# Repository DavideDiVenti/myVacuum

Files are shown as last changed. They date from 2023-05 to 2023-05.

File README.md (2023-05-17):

# myVacuum
La conception d'un projet s'est déroulé dans le cadre d'un cours de bureaux d'études. Le projet en question est un aspirateur digital. 
Le rendu 3D du projet peut être directement visionné en cliquant sur [ce lien hypertexte](https://a360.co/3LSl4pl) (ouvrez ensuite *depuis le navigateur*).

## Introduction
Le projet en question consiste en un aspirateur doté de fonctionnalités numériques supplémentaires. Comme tout aspirateur domestique, il a pour fonction principale d'aspirer les miettes, la poussière, le sable, etc. Toutefois, contrairement à ses homologues, myVacuum est capable de fournir à son utilisateur un état de santé en temps réel grâce à un écran. Cet état inclut des informations telles que la température interne de l'appareil, le niveau de remplissage du réservoir, la qualité de l'air aspiré, la vitesse du ventilateur, et bien d'autres encore.

L'utilisateur peut contrôler l'aspirateur à partir d'une interface utilisateur. Cette dernière prend la forme d'une télécommande filaire équipée d'un petit écran et de 4 boutons poussoirs. L'interface comprend plusieurs menus préprogrammés, notamment une zone permettant de visualiser et de commander l'état de l'appareil (puissance d'aspiration), ainsi qu'une autre zone permettant d'acquérir des données et de créer des graphiques des données lues par les capteurs en temps réel. 

## Le répertoire [*myVacuumCode*](https://github.com/DavideDiVenti/myVacuum/tree/main/myVacuumCode)
### Code du microcontroleur
L'aspirateur intègre le microcontrôleur ESP32. Les codes téléversés sont dans le répertoire [myVacuumCode](https://github.com/DavideDiVenti/myVacuum/tree/main/myVacuumCode). Ce-dernier assemble tous les périphériques de l'aspirateur (voir [Rapport](https://github.com/DavideDiVenti/myVacuum/blob/main/Documents/Rapport.pdf)) afin de centraliser le tout.

### Design de l'écran
A noter que le rendu final du projet n'aurait pas pu etre possible sans l'utilisation d'un logiciel en particulier. Ce logiciel est un ancien projet que j'ai développé expressément pour l'aspirateur : 
* L'idée de ce logiciel est que l'utilisateur puisse créer des icones et animations de ces-derniers en pixelart. 
* A chaque interraction le logiciel exporte l'image sous forme d'une chaine hexadécimale et/ou binaire. 
* L'utilisateur peut ensuite copier cette chaine et l'introduire dans le code de son microcontroleur.
* Le code du microcontroleur interpretera cette chaine hexadécimale ou binaire afin de créer des objets de classe respectif à chaque chaine (icone d'un ventilateur, d'un termomètre, d'un buzzer, ...). 
* La [classe](https://github.com/DavideDiVenti/myVacuum/blob/main/myVacuumCode/myClass_DrawOnTheScreen.cpp) pourra ensuite proposer divers méthodes afin d'afficher les pixels sur l'écran correspondant à l'objet en question.

Ce processus permet notamment de créer des animations de plusieurs frames d'un meme objet :
<p align="left">
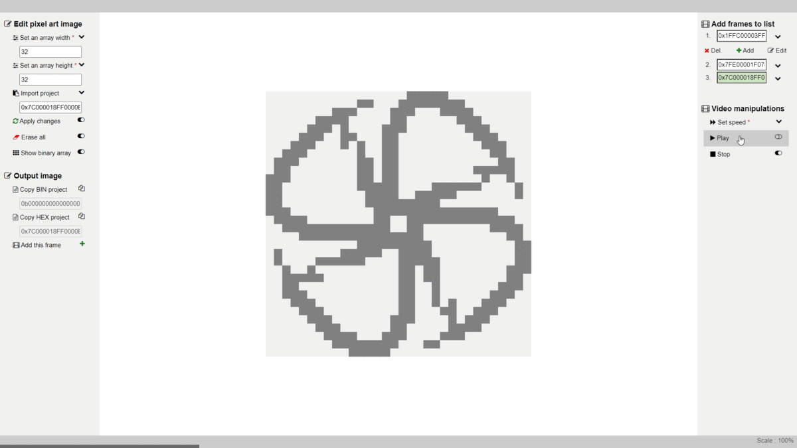
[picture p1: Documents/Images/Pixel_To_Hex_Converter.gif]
  
</p>
Le logiciel est disponible depuis ce lien : https://davidediventi.github.io/PixelToHexConverter/

## Le répertoire [*Documents*](https://github.com/DavideDiVenti/myVacuum/tree/main/Documents)
Divers documents sont situés dans ce répertoire [Documents](https://github.com/DavideDiVenti/myVacuum/tree/main/Documents). Des informations supplémentaires s'y trouvent :
* Un dossier [Impressions_3D](https://github.com/DavideDiVenti/myVacuum/tree/main/Documents/Impressions_3D) contenant l'entièreté des fichiers d'impression au format stl. 
* Un dossier [Images](https://github.com/DavideDiVenti/myVacuum/tree/main/Documents/Images) contenant quelques aperçuts finaux du projet (PCB, Mécanique, Schémas, ...).
* Un fichier [Rapport](https://github.com/DavideDiVenti/myVacuum/blob/main/Documents/Rapport.pdf) correspondant au rapport du projet sous le format pdf. Dedans se trouve l'entièreté du contenu (schémas, développements techniques, ...) ainsi qu'un tableau des pinouts de l'ESP32.

## Youtube
Il est toujours plus ludique d'observer le projet sous forme de vidéos.

### Démonstration du projet :
Dans cette vidéo, l'aspirateur aspire plusieurs type de déchets (copeaux d'aluminium, terre, copeaux de bois, ...).

Vidéo postée prochainement...

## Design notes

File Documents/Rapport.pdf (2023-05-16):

## MYVACUUM, L’ASPIRATEUR INTELLIGENT

Conception Mécanique, Électronique, Traitement De Signal, Programmation, …

### Par DI VENTI Davide 60456@etu.he2b.be

RÉSUMÉ

Le projet en question consiste en un aspirateur doté de fonctionnalités numériques supplémentaires. Comme tout aspirateur domestique, il a pour fonction principale d'aspirer les miettes, la poussière, le sable, etc. Toutefois, contrairement à ses homologues, myVacuum est capable de fournir à son utilisateur un état de santé en temps réel grâce à un écran. Cet état inclut des informations telles que la température interne de l'appareil, le niveau de remplissage du réservoir, la qualité de l'air aspiré, et bien d'autres encore.

L'utilisateur peut contrôler l'aspirateur à partir d'une interface utilisateur. Cette dernière prend la forme d'une télécommande filaire équipée d'un petit écran et de 4 boutons poussoirs. L'interface comprend plusieurs menus préprogrammés, notamment une zone permettant de visualiser et de commander l'état de l'appareil, ainsi qu'une autre zone permettant d'acquérir des données et de créer un système de logs¹
à partir d'une carte SD.

Tout comme les aspirateurs domestiques classiques, myVacuum est équipé d'une fonction permettant de régler la puissance d'aspiration. Toutefois, contrairement aux autres modèles, cette fonction est entièrement numérique, ce qui la rend plus précise. De plus, il dispose d'un tachymètre intégré qui fournit un retour sur la vitesse du ventilateur.

### 1. INTRODUCTION

Ce rapport présente la conception et la réalisation d'un aspirateur digital, en mettant l'accent sur les différentes parties mécaniques, électroniques et de programmation du système. La partie mécanique est abordée en premier lieu, en décrivant la conception de pièces spécifiques telles que des adaptateurs en plastique et en métal. Ensuite, la partie électronique est examinée, mettant en lumière les choix de composants ainsi que le traitement du signal du capteur, un point central du projet. Le traitement du signal est effectué en utilisant des principes tels que le filtrage, l'amplification et le registre à décalage. Enfin, la partie programmation est présentée en détail, expliquant le fonctionnement final du code et incluant un lien vers le dépôt GitHub où celui-ci est disponible. Des schémas électroniques et

1Logs : Sous forme d’un tableau, il s’agit d’une suite séquentielles de valeurs acquises par des capteurs ou autre en fonction du temps. Cela peut se référer à un historique. Chaque données est stockée tous les laps de temps.

mécaniques détaillés du système sont également fournis dans les annexes du rapport.

L'objectif premier de ce rapport est de présenter un produit sortant d'un bureau d'études, qui intègre des systèmes embarqués de manière technique.

### 2. DESCRIPTION DU PROJET

Le projet est subdivisé en quatre grandes parties distinctes. Chacune de ces parties a nécessité des prérequis spécifiques ainsi qu'une durée de conception relativement similaire à celle des autres parties.

### 2.1. Mécanique

La mécanique est un aspect essentiel de ce projet. Chaque élément a été préalablement conçu en 3D, allant des différents adaptateurs jusqu'aux joints d'étanchéité. Les adaptateurs, qui sont imprimés en 3D en PLA, ont été créés pour servir de supports pour les capteurs, pour les systèmes d'emboîtement (entre filtre, ventilateur, réservoir, tube d'aspiration, etc.), pour les connecteurs électroniques avec détrompeurs, etc. Le filtre, pour sa part, est également imprimé en 3D. Sa structure est conçue pour accueillir un tissu carbonisé servant de filtre à air. De même, l'interface utilisateur possède un socle imprimé en 3D. Les joints d'étanchéité sont également imprimés, mais cette fois-ci en TPU, un caoutchouc adapté pour l'extrusion des imprimantes 3D.

En outre, j'ai utilisé une CNC pour découper une pièce : il s'agit d'une plaque en acrylique positionnée à la base du filtre. Cette plaque permettra à un capteur de pouvoir émettre une lumière et recevoir sa réflexion tout en étant protégé des déchets dans le réservoir (capteur de niveau de remplissage du réservoir). Le réservoir de l'aspirateur est également fabriqué en acrylique. Il s'agit d'un tube cylindrique de 100 mm de diamètre.

Enfin, une fois toutes ces pièces assemblées, j'ai remarqué que l'aspirateur avait tendance à tomber latéralement à plusieurs reprises. J'ai donc été contraint de trouver une solution, et j'ai décidé de concevoir un socle en aluminium à l'aide d'un tour à métaux. Cette pièce s'emboîte dans le bas du réservoir, permettant ainsi de fermer le réservoir et de descendre le centre de gravité de l'aspirateur. Cette solution a été la plus adaptée et satisfaisante pour moi, étant passionné depuis mon enfance par l'usinage de pièces industrielles.

En prenant en compte le temps de conception de chaque pièce mécanique (temps d'impression 3D non inclus), cela représente plus de 22 heures de travail.

### 2.2. Électronique

Dans ce projet, l'électronique utilise une architecture basée sur une unité de contrôle. Cette carte électronique
centralise | les | données | provenant | de | différents
périphériques tels que les capteurs, le ventilateur et l'écran, pour les traiter, les afficher, les stocker, etc.

Un microcontrôleur ESP32 a été choisi pour cette unité de contrôle. Toutes les broches du microcontrôleur ont été utilisées afin de tirer pleinement parti de ses capacités. L’annexe 7 présente les périphériques connectés (ou transistorisés) à ce microcontrôleur, je vous invite à la prendre.

Chaque périphérique est justifié et joue un rôle crucial dans le cadre de ce projet. Le buzzer permet d'alerter l'opérateur en cas de détection d'un code d'erreur. Par exemple, si l'aspirateur aspire de la matière brûlée (détectée par le DHT11 et le capteur de gaz MQ-2), de la matière humide (par le DHT11), ou un gaz nocif pour la santé humaine (par le capteur de gaz MQ-2), le buzzer émet une alerte. D'autres situations peuvent également survenir, telles que le remplissage du réservoir (capteur de distance VL6180X), la nécessité de nettoyer le filtre (vitesse du ventilateur trop faible), ou encore la saturation de la carte SD.

Le relais fonctionne selon le même principe que celui intégré dans les aspirateurs industriels, à savoir une prise 230VAC destinée à connecter une machine-outil telle qu'une scie sauteuse, une foreuse ou une défonceuse. En d'autres termes, si le périphérique 230VAC est activé, l'aspirateur s'allume. Dans le cas de myVacuum, ce principe est repris, mais sous une forme miniaturisée avec un relais.

Le ventilateur utilisé (bg0903-b049-p0s) provient d'un PC Dell fixe où il occupait la place du ventirad. L'ensemble du projet est dimensionné en fonction de ce ventilateur, qui est un ventilateur 12VDC comportant 4 broches dont deux pour l'alimentation 12V, une pour le tachymètre, et une pour la commande PWM. Le « Fan MOSFET » affiché dans l’annexe 7 du ventilateur, est un simple transistor MOSFET que j’ai ajouté permettant de couper ou de fournir l'alimentation 12V externe au ventilateur. En effet, même en forçant un état logique bas (0V) à la commande PWM du ventilateur, sa vitesse (tr/min) ne descend pas à zéro, mais atteint plutôt un seuil minimum de XX tr/min.

En prenant en compte le temps nécessaire à la réflexion (choix des composants) et à la conception électronique (schémas électroniques et conception du PCB), le temps total de travail estimé s'élève à plus de 16 heures.

### 2.3. Traitement de signal

Le traitement du signal réalisé dans ce projet est la partie la plus électronique de la machine concernée. Il est effectué à la sortie du tachymètre du ventilateur, de manière à ce que l’ESP32 puisse lire la vitesse sans qu'il y ait de nombreuses erreurs ni de latences. Les étapes suivantes décrivent le dimensionnement des étages de traitement du signal tachymètre.

Avant toute chose, il convient de noter que ce ventilateur envoie 2 signaux logiques par tour.

Le premier étage de traitement du signal vise à transmettre ces signaux avec une logique de 0V à 3,3V (ce qui n'est pas le cas par défaut). Étant donné que le capteur intégré est à effet Hall, l'intensité du signal tachymètre varie en fonction de la vitesse. Plus la vitesse est élevée, plus l'intensité du signal augmente en tension (de 0 à 1,8V), ce qui peut perturber la lecture de la vitesse. Il est donc nécessaire de procéder à un étage d'amplification. Toutefois, avant cela, il est préférable de filtrer les parasites potentiels (pics de tension à très
haute | fréquence) | susceptibles | de | "brouiller"
l'amplification. Pour ce faire, un simple filtre passe-bas RC est suffisant. 'ai dimensionné le filtre de telle sorte que la fréquence de coupure soit d'environ 5 kHz, qui est la fréquence maximale du tachymètre du ventilateur. Ensuite, par expérimentation, j'ai essayé différentes valeurs de R et C pour obtenir une enveloppe de signal filtré adaptée à mes besoins, finalement en utilisant C = 50 nF et R = 2 kΩ, j'ai obtenu un filtrage opérationnel.

Une fois le filtrage terminé, j'ai procédé à l'amplification en utilisant un amplificateur opérationnel (AOP) que j'ai utilisé en tant que comparateur, tel un trigger de Schmitz. Étant donné que le signal filtré possédait un offset de 400 mV, il était important d'éliminer cet offset avant l'amplification. Pour ce faire, j'ai utilisé une tension de référence provenant d'un pont diviseur de tension pour éliminer l'offset par le biais du V- de l'AOP, évitant ainsi que l'offset ne s'amplifie. La tension de référence a été fixée à 800 mV pour garantir que l'offset ne serait pas pris en compte à la sortie du comparateur. Le signal filtré du tachymètre (V+) et la tension de référence (V-) ont été comparés, et seule la tension supérieure à 800 mV a été copiée en sortie. Le signal de sortie du comparateur a atteint un niveau logique équivalent à l’alimentation de l’AOP (0V-3.3V).

Cependant, une problématique persiste en dépit de l'aspect impeccable du signal, carré et net. En effet, la vitesse du signal demeure trop rapide pour être traitée de manière satisfaisante par l'ESP32. Bien que le microcontrôleur puisse traiter et convertir la vitesse du signal en tr/min, un facteur important doit être pris en compte : la latence du programme. À mesure que le programme gère davantage de périphériques, des latences se produisent, entraînant un délai de quelques millisecondes à la fin de la boucle. Une latence de quelques millisecondes (1ms à 20ms) est considérable, surtout si le microcontrôleur doit lire un signal à haute fréquence. L'oscilloscope a mesuré une fréquence de 1250Hz pour le signal filtré et amplifié, ce qui correspond à une période de signal de 800µs. Cela équivaut à une vitesse de rotation du ventilateur de 5500 tr/min.

Un deuxième étage de traitement de signal s’est donc imposé, celui permettant de diminuer la fréquence du signal, tout en restant beau, carré et propre. Pour ce faire, il n’y a rien de plus efficace que de l’électronique ancienne : le registre à décalage. J'ai disposé d'un registre à 8 bits, ce qui m'a permis de diviser la fréquence du signal par 8, résultant en une période de 6,4 ms au lieu de 800 µs. Cette solution est largement suffisante pour mon application. Afin d'assurer le bon fonctionnement de cette idée subite, j'ai simulé ce principe et procédé à plusieurs essais et erreurs. Heureusement, le résultat a été couronné de succès.

En outre, compte tenu du temps nécessaire à l'étape de dimensionnement et aux tests requis pour ces traitements de signaux, le temps total de travail s'élève à plus de 11 heures.

### 2.4. Programmation

Dans le but d'améliorer la compréhension et la simplicité du code, j'ai procédé à l'importation de la bibliothèque Arduino. Cette démarche m’évite de concevoir mes propres méthodes de classe pour effectuer des opérations élémentaires, telles que l'attribution d'une broche en tant que sortie ou entrée, l'affichage de données dans la console et la gestion des interruptions, etc.

2.4.1. Affichage dans l’écran TFT

En complément de cette bibliothèque, le code est doté d'une classe que j'ai élaborée. Cette dernière me permet de créer des icônes et des animations personnalisées sur l'écran TFT. L'objectif est de pouvoir générer plusieurs objets (widgets : icône de ventilateur, icône de thermomètre, ...) et les afficher avec la latence la plus minimale possible.

Afin d'atteindre cet objectif, je n'enregistre pas les images au format PNG, JPG ou autre sur la carte SD, mais plutôt dans un format personnalisé et léger : une chaîne de caractères. À partir de cette chaîne, ma classe décode les données et affiche l'image correspondante pixel par pixel en couleur.

La déclaration de la chaîne de caractères est précédée par les dimensions (en pixels) de l'image à afficher :

int myIconeWidth, myIconeHeight = 16, 16;

String myIcone = "7C00820101014901490FF96 805DFE41407D3F8510851079080206EC02A80444";

Ensuite, ces trois variables sont insérées pour la création de l'objet de ma classe. La chaîne hexadécimale est ensuite convertie en binaire, ce qui entraîne une augmentation de sa longueur quatre fois supérieure. Ligne par ligne et colonne par colonne, la chaîne binaire est parcourue, et la classe affiche des pixels aux coordonnées correspondantes là où des "1" sont présents, tandis qu'elle n'affiche rien là où des "0" sont présents (comme illustré ci-dessous dans la figure 1) :

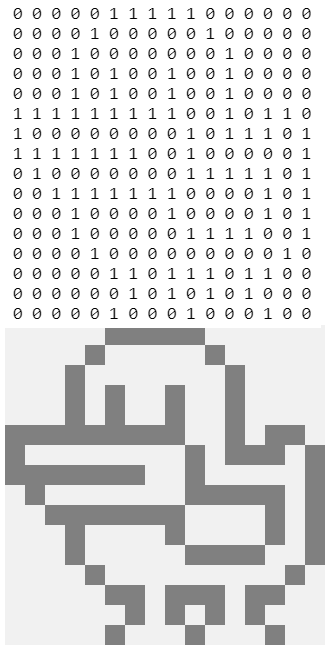
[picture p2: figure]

Figure 1. Processus d’affichage dans l’écran TFT

Cependant, il n'est pas possible pour un être humain d'écrire intuitivement cette chaîne de caractères. Il est donc nécessaire d'effectuer l'inverse du processus. À cet effet, j'ai développé un logiciel en JavaScript qui me
permet | de | générer | la | chaîne | de | caractères
hexadécimale/binaire à partir d'un espace de travail de dessin en PixelArt. Les détails de fonctionnement de ce logiciel ne seront pas abordés dans ce rapport, car cela s'éloignerait du sujet principal. J'ai hébergé ce logiciel sur GitHub, et il est directement accessible via le lien suivant :

https://davidediventi.github.io/PixelToHexConverter/

Le plus grand défi de ce projet a été de surmonter les latences du microcontrôleur, et cette classe combinée à ce logiciel ont joué un rôle clé pour résoudre ce problème.

2.4.2. Acquisitions de données des capteurs

En parallèle de l'affichage, il y a également l'acquisition de données. Quatre des cinq données à acquérir sont actualisées à intervalles réguliers de 300 ms. Ces données comprennent la température (°C), l'humidité (%), la qualité de l'air (%) et le niveau de remplissage du réservoir (mm). Quant à la cinquième donnée, qui correspond à la vitesse du ventilateur, elle est acquise d'une manière différente.

En effet, sur une période de 1800 ms, l'ESP32 compte le nombre de tours effectués par le ventilateur à l'aide d'interruptions externes. Ensuite, une conversion est effectuée pour obtenir les tours par minute (rpm).

Ces | données | sont | affichées | dans | le | menu
DASHBOARD, précédées des icônes correspondantes telles que le thermomètre, la goutte d'eau, le compteur, etc. Elles sont également affichées dans le menu LOGS de l'écran, mais cette fois-ci sous forme de graphique en temps réel.

Les graphiques présentés dans le menu LOGS conservent un historique de données sur une période de 30 secondes, correspondant à une largeur de courbe de 100 pixels. En d'autres termes, toutes les 300 ms, une acquisition est effectuée, et un pixel est affiché à une échelle commune pour tous les capteurs. Donnée par donnée, pixel par pixel, une courbe prend forme. Toutes les courbes de tous les capteurs sont regroupées dans un même graphique en temps réel.

2.4.3. Carte SD

Toutes les 3 secondes, il y a une écriture sur la carte SD. Les données sont enregistrées sous forme d'un fichier CSV contenant cinq colonnes correspondant aux cinq données pouvant être acquises : la température (°C), l'humidité (%), la qualité de l'air (%), le niveau de remplissage du réservoir (mm) et la vitesse de rotation du ventilateur (rpm).

À chaque démarrage de l'aspirateur, un nouveau fichier CSV est créé. Cela permet ensuite de lire les données sur un ordinateur à l'aide d'un logiciel tel qu'Excel. En créant des graphiques à partir de ces valeurs, il devient possible de diagnostiquer d'éventuels défauts de la machine.

Bref, en prenant en compte le temps consacré au développement du code, le travail total s'élève à plus de 60 heures (le logiciel pixelart n'étant pas inclus).

### 3. MATÉRIEL & MÉTHODES

Ce projet n'aurait pu être mené à bien sans l'accès au matériel adéquat et aux prérequis nécessaires. Plusieurs outils sont mis à disposition des étudiants et j'en ai profité.

### 3.1. Outils utilisés

Parmi les nombreux outils indispensables pour mener à bien ce projet, je possède certaines machines à mon domicile, ce qui m'a grandement facilité la tâche pour poursuivre le travail à distance.

3.1.1. Outils mécaniques

Le Fablab de l'école met à disposition des étudiants des imprimantes 3D Prusa. Pour imprimer en 3D, il est nécessaire de générer les fichiers STL de la pièce en 3D depuis un logiciel de modélisation 3D, puis de les donner à un préparateur afin qu'il génère le GCode à partir du slicer approprié. J'ai personnellement utilisé Fusion 360 comme logiciel de modélisation 3D. Par ailleurs, des machines à commande numérique (CNC) sont également disponibles, notamment la machine Mekanika qui est particulièrement appréciée. En ce qui concerne l'usinage industriel, j'ai eu recours à un tour à métaux Celtic 14 mis à disposition par l'école, qui est un modèle de grande qualité.

3.1.2. Outils électroniques
Pour | visualiser | les | signaux | électriques, | un
oscilloscope est indispensable. J'ai utilisé le modèle Tektronix TDS 2014B tout au long de l'étude de dimensionnement des étages de traitement de signal de mon projet à l'école.

Une fois que j'ai validé l'électronique sur une platine d'expérimentation, j'ai conçu le PCB à l'aide du logiciel Fusion360. Cette étape m'a permis de générer les fichiers Gerber, nécessaires pour fabriquer le PCB chez JLCPCB, un fabricant de circuits électroniques.

3.1.3. Outils informatiques

Pour la programmation de l'ESP32, j'utilise l'IDE Arduino. Cette interface de développement logiciel propose une arborescence simple et efficace, adaptée à mes besoins. Pour stocker les données collectées, l’aspirateur édite des fichiers CSV sur une carte SD. Cette méthode facilite la visualisation et l'analyse des données sur un ordinateur, grâce notamment à la
création | de | graphiques. | Cet | outil | se | révèle
particulièrement utile lorsqu'il s'agit de diagnostiquer

d'éventuels | dysfonctionnements | rencontrés | par
l'aspirateur lors de sa mise en service.

### 3.2. Méthodes d’avancement de l’étude

Il n'existe pas de méthode ou de technique universelle pour la conception de projets. Il est nécessaire de se connaître soi-même et de déterminer la durée estimée de chaque tâche avant de s'engager dans une étape dont la fin ne nous est pas clairement définie.

En tant que maker né, j'ai acquis une expérience qui me permet de mener à bien chacun de mes projets dans les délais impartis. Cependant, chaque projet est unique et nécessite une méthode d'avancement différente en fonction de ses spécificités. La méthode à utiliser doit s'adapter au contenu du projet.

La réussite de cette méthode est conditionnée par la nécessité de connaître au préalable le rendu final du premier prototype. Pour atteindre ce stade, il est impératif que le projet nous motive et nous fasse rêver. Dans mon cas, la motivation est atteinte lorsqu'il y a une intégration de la mécanique. Mais ma condition première est que le projet doit avoir une utilité en dehors du monde académique (s’il s’agit d’un projet scolaire).

L’idée de concevoir un aspirateur m’est lointaine. Mais, je n'avais pas encore discerné l'utilité d'un aspirateur personnel. En effet, mes projets personnels se multiplient au fil du temps. À présent, j'en suis arrivé au stade où je conçois une CNC semi-professionnelle pour un usage domestique. Le but de cette machine est de découper de l'aluminium pour des projets à venir. Et qui dit CNC, dit aspirateur. Le tube d'aspiration sera relié à la broche du routeur de la machine pour aspirer les copeaux. Lorsque la fraise se met à tourner, l'aspirateur se déclenche. Pour ce faire, la CNC communiquera en UART avec l'aspirateur (des headers mâles sont prévus dans le PCB : UART2). Telle est donc l'idée qui m'a inspiré pour mener à bien ce projet.

Pour ce projet, j'ai estimé qu'il serait plus judicieux de travailler en parallèle sur toutes les parties du projet (mécanique, électronique et programmation) tout en gardant à l'esprit les objectifs finaux. Telle a été ma méthode.

J'ai donc commencé par dessiner un croquis sur papier, qui incluait l'idée finale du projet selon mes réflexions. J'ai transmis ce croquis ainsi que le cahier des charges aux professeurs en charge du projet concerné, trois mois avant le début du premier cours. Une fois qu'ils ont validé l'idée du projet, je me suis lancé directement dans sa conception.

### 3.3. Étapes de la réalisation du projet

Le premier cours du projet a débuté le 1er février 2023. Quant au dernier, il a eu lieu le 22 mai 2023. Dans la table 1 se trouve l’avancement du projet en fonction des semaines académiques, en commençant par la semaine -1, qui est celle précédée du premier cours :

Semaine | Avancement
-1 | Commande PWM du ventilateur avec un
potentiomètre. Affichage de la vitesse sur l’écran TFT.
1 | Assemblage | de | quelques | capteurs/
actionneurs dans un même programme. Modélisation 3D du ventilateur.
2 | Ajout du capteur de distance dans le
programme. | Premières | étapes | du
traitement de signal du tachymètre.
3 | Réalisation de l’interface utilisateur
(UI)(impression 3D + soudage PCB + usinage des boutons poussoirs).
4 | Impressions 3D des adaptateurs et du
filtre. | Premiers | tests | avec | tube
d’aspiration.
5 | Connectiques des capteurs dans le filtre
et premiers tests sur leur support.
6 | Usinage du socle en aluminium.
7 | Finalisation des étages du traitement du
signal du tachymètre.
8 | Changements de plan sur le type de tube
d’aspiration. Débogage et correction d’une mauvaise compatibilité entre périphériques SPI (section 4.).
9 | Conception du PCB principale.
10 | Corrections des problèmes du PCB.
11 | Développement du programme et de
tous les systèmes embarqués de l’UI.
12 | Finalisation et rédaction du rapport.

Table 1. Étapes de la réalisation du projet

### 4. PROBLÈMES RENCONTRÉS

Dans cette section, seuls les problèmes les plus importants rencontrés lors de la réalisation du projet seront abordés. Bien que d'autres problèmes aient été identifiés, ils ont eu moins d'impact sur l'avancement global du projet et ne seront pas traités ici.

### 4.1. Plusieurs périphériques SPI dans un même bus

Comme évoqué dans la section précédente, lors de la huitième semaine de travail sur le projet, j'ai identifié et corrigé un problème important qui avait été négligé jusqu'alors. Ce problème affectait mon module ST7735, qui est responsable de l'affichage sur l'écran TFT ainsi que de la gestion de la carte SD. Bien que la fonctionnalité combinée de ces deux éléments soit très pratique, j'ai rapidement découvert que les deux ne pouvaient pas fonctionner sur le même bus SPI.

Bien | que | j'ai | pu | faire | fonctionner | l'écran
indépendamment, j'ai rencontré des conflits de bibliothèques lorsque j'ai essayé de combiner l'écran et la carte SD, ce qui m'a empêché de lire ou écrire sur cette dernière. Après des recherches approfondies, je n'ai trouvé aucun tutoriel ou forum expliquant comment faire fonctionner les deux éléments ensemble. Je tournais en boucle, cela ne servait à rien.

J'ai pris l'initiative de remédier à ce problème par mes propres moyens. Après avoir étudié les datasheets de l'écran et de la carte SD, j'ai découvert que les deux périphériques ne fonctionnaient pas sous la même fréquence d'horloge SPI. En effet, l'écran fonctionne à une fréquence de 20 kHz, ce qui est extrêmement faible pour un bus SPI, tandis que la carte SD fonctionne sous une fréquence de 4 MHz. Par conséquent, il n'était pas possible de les faire fonctionner sur le même bus SPI, ce qui m'a contraint à créer deux bus SPI indépendants dans le circuit.

Après avoir connecté et reprogrammé tous les composants, j'ai constaté que l'écran fonctionnait correctement, mais pas la carte SD. Toutefois, je savais pourquoi cette fois-ci. En effet, avec le même code et un lecteur de carte SD externe, les deux périphériques fonctionnaient mutuellement. J'en ai donc déduit qu'il y avait une mauvaise compatibilité de tensions logiques entre l'ESP32 et le lecteur de carte SD du modèle ST7735. Après une analyse minutieuse, j'ai remarqué que sur le PCB de ce module, des résistances abaisseuses de tension étaient placées pour les broches SCK, MISO et MOSI. Par conséquent, j'ai déduit que ce module était conçu pour une tension logique de 5V plutôt que de 3V3.

J'ai donc court-circuité les résistances du module, mais malgré cela, la carte SD ne fonctionnait toujours pas. J'ai immédiatement compris pourquoi. Juste à côté des résistances se trouvait un régulateur de tension de 3V3 qui alimentait la carte SD. Hors, en entrée de ce régulateur, il convient de fournir une tension de 5V, et non de 3V3. J’en ai conclu que ce module ST7735 était dimensionné pour les Arduino (travaillant sous du 5V), et non les ESP32 (travaillant sous du 3V3). C'est pourquoi j'ai procédé à la suppression de ce régulateur, en réalisant un court-circuit entre son entrée et sa sortie, permettant ainsi de fournir directement une tension de 3V3 à la carte SD. Cette modification a permis de résoudre le problème de compatibilité entre l'ESP32 et le lecteur de carte SD du ST7735.

Le dépannage de cette problématique a nécessité une durée de plus de quatre heures, impactant ainsi négativement ma soirée. Toutefois, l'issue positive de la situation m'a permis de passer une nuit paisible.

### 4.2. Le choix du microcontrôleur

À ce stade de la lecture de ce dossier, vous avez certainement une idée précise sur le sujet et avez déjà formé votre opinion. Cependant, il est important pour moi de mentionner un détail qui a peut-être traversé votre esprit, mais que je n'ai pas encore abordé :

« Pourquoi utiliser l'ESP32 sans exploiter sa connexion WLAN ? »

En effet, l'ESP32 est capable d'exécuter des tâches WLAN telles que le Wifi 2,4 GHz et le Bluetooth 2,4 GHz. Vous pourriez alors objecter :

« C'est comme utiliser une GoPro² pour prendre des photos banales. »

En effet, je reconnais que l'utilisation de la GoPro dans ce contexte serait peu judicieuse. Toutefois, ma situation présente des particularités qui ne sauraient être comparées à ce cas de figure.

En partant du principe que vous avez raison et que le microcontrôleur actuel doit être remplacé par un autre plus adapté, j'ai mené une petite étude, qui a conduit au choix du microcontrôleur STM32 comme solution idéale pour le présent projet, étant donné l'absence de connexion WLAN. En effet, il s'avère être moins surdimensionné qu'un ESP32, tout en offrant des performances surprenantes. Avec une fréquence CPU de 72 MHz, presque équivalente à celle de l'ESP32 (160 MHz), un nombre de broches d'entrée/sortie de 37 (contre 36 pour l'ESP32), et surtout une capacité à gérer les interruptions de manière beaucoup plus performante que l'ESP32, il présente toutes les caractéristiques nécessaires pour ce projet [2].

Je suis conscient que le choix du microcontrôleur est un sujet délicat, qui nécessite des justifications argumentées. Cependant, il est important de rappeler que ce projet n'est pas un produit fini, mais un prototype. Les améliorations les plus fréquentes d'un prototype sont d'abord de nature matérielle, mais par la suite, c'est le logiciel qui ne cesse de se mettre à jour.

Dans l'hypothèse où le matériel resterait tel quel, c'est-à-dire que le PCB ne serait pas modifié, il serait toujours possible d'améliorer le produit en termes de logiciel. En effet, à ce stade, je pourrais débloquer la connexion WLAN et concevoir des applications typiques de l'IoT³
. Si j'avais choisi le STM32 pour ce projet, pour procéder à ce type d'amélioration, j'aurais dû modifier le PCB pour y intégrer un module WLAN supplémentaire, ce qui n'est pas rentable. En revanche, l'ESP32 peut tout faire en un seul module.

2GoPro : caméra dotée d’une protection la rendant résistante aux chocs et étanche. Ultra polyvalente et tellement petite qu’elle tient dans la poche (prix compris entre 300 & 400€) [1].

3
IoT : Internet of things, ou Internet des Objet en français. L’IoT reflète les objet connectés équipés de capteurs et actionneurs accessibles à distance depuis des logiciels et autres [3].

### 5. RÉSULTATS FINAUX

Les résultats finaux de ce projet ont été un vrai succès. Le produit a pu respecter l’entièreté des critères du cahier des charges.

### 5.1. GitHub

J'ai mis à disposition ce projet sur un dépôt GitHub afin de le rendre accessible aux personnes les plus curieuses d'entre vous. Si vous désirez obtenir des informations techniques supplémentaires, ce dépôt est tout indiqué :

https://github.com/DavideDiVenti/myVacuum

### 5.2. Résultats finaux mécaniques

En ce qui concerne la partie mécanique de ce projet, des images sont plus explicites que des mots. Je vous invite donc à consulter l’annexe 4 pour avoir une meilleure compréhension. Dans le dépôt GitHub cité dans la section 5.1 de ce rapport se trouve également des informations supplémentaires, notamment un site web (propre à Fusion 360) où il nous est possible visualiser en 3D le projet en ligne.

Je tiens à souligner que chaque partie du projet a été conçue intégralement par mes soins, en utilisant mon expérience et mon imagination dans le domaine. Les seules pièces qui n'ont pas été conçues par moi-même sont le réservoir (ou plutôt le tube en acrylique transparent de diamètre 100 mm, que j'ai acheté), le ventilateur (que j'ai récupéré d'un vieux PC) et le tissu carbonisé servant de filtre à air (que j'ai acheté). La visserie a également été achetée. Pour le reste, j'ai utilisé des matières premières et j'ai fabriqué les pièces nécessaires moi-même.

Un élément clé qui n'a pas encore été discuté est l'architecture de l'aspirateur. Chaque composant est minutieusement placé, avec une justification précise pour chaque emplacement. Il est conseillé d'avoir l'annexe 4 à portée de main avant de décrire chaque emplacement des composants.

L'aspirateur est soutenu par quatre pieds en caoutchouc, fixés sur une base en aluminium. Le réservoir, un tube en acrylique transparent de 100 mm de diamètre, est emboîté dans cette base. Pour assurer une étanchéité adéquate, un joint en TPU est intercalé entre les deux éléments. À côté du tube transparent se trouve un orifice destiné au tube d'aspiration. Pour fixer le tube, un adaptateur est fixé à l'orifice, également équipé d'un joint. Le tube d’aspiration vient se visser dans cet adaptateur. Dans l'opposé de cet orifice, un autocollant en vinyle portant l'inscription myVacuum est apposé sur la circonférence du réservoir.

Au-dessus du réservoir, un adaptateur permet de fixer le filtre et le ventilateur. Le filtre contient trois supports pour les capteurs (DHT11, MQ-2 et VL6180X), le dernier étant dirigé vers le bas pour mesurer le niveau de remplissage du réservoir. Une plaque en acrylique transparente est placée entre le fond du réservoir et la base du filtre pour permettre la transmission de la lumière des capteurs tout en protégeant le capteur des déchets. Cette plaque est fixée à la base du réservoir.

Le support du PCB se trouve sur le ventilateur, qui est conçu pour épouser la même forme visuelle que le ventilateur. Le connecteur de l'interface utilisateur est branché sur le PCB. Cette interface portable, mais avec fil.

L'interface utilisateur est dotée de quatre pieds en caoutchouc et fixée sur une base rectangulaire en aluminium. Quatre entretoises sont vissées sur cette base pour accueillir le PCB de la manette. Un couvercle en PLA est ensuite clipsé sur le PCB pour renfermer l'électronique, n'exposant que l'écran, l'accès à la carte SD et les boutons-poussoirs. Des extensions en aluminium ont été usinées pour les boutons-poussoirs, leur permettant ainsi d'être accessibles depuis l’extérieur du couvercle.

### 5.3. Résultats finaux électroniques

Dans la partie électronique se trouve l'étape de traitement du signal du tachymètre. La figure 2 ci-dessous illustre l'ensemble des étapes du traitement du signal, depuis sa capture initiale jusqu'à son traitement final :

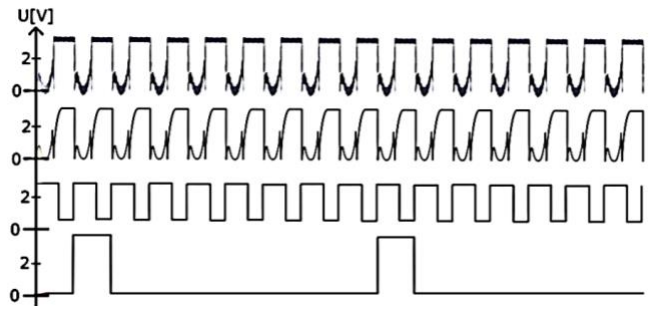
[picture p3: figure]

Figure 2. Signaux filtrés d’étage en étage

Il s'agit ici du signal correspondant à la vitesse maximale du ventilateur. Plus la vitesse est réduite, moins l'intensité des interférences est élevée. Le signal n°1 est celui issu du ventilateur. À chaque impulsion carrée (pulled up par une résistance que j'ai ajoutée), le signal en question est précédé. Ce dernier est généré par le capteur à effet Hall et sa forme est évolutive et croissante dans le temps, jusqu'à ce que le capteur ne soit plus dans la portée magnétique du pôle encastré dans l'axe rotatif du ventilateur. Dans ce signal se trouvent donc deux signaux indépendants, l'un étant celui généré par le capteur à effet Hall, et l'autre, qui le suit, étant celui de la résistance tirée vers 3V3. Ce signal carré de 3V3 est tiré vers le haut dès l'instant où le capteur à effet Hall sort de la portée magnétique du pôle de l'axe du ventilateur. Et c'est ce signal carré qui sera exploité tout au long du traitement du signal.

Le signal n°2 est celui filtré par le filtre passif passe-bas RC. Ce signal se différencie du premier par sa forme plus douce et atténuée.

Le signal n°3 est celui de la sortie de l'amplificateur opérationnel utilisé comme comparateur, tel un trigger de Schmitz. Le signal « offset » généré par le capteur à effet Hall est ainsi neutralisé, de sorte à avoir uniquement le signal carré 0V-3V3.

Quant au signal n°4, il s'agit du signal final. Une fois que le signal n°3 est passé par le registre à décalage 8 bits, sa fréquence est divisée par 8. Ce sera ce signal qui sera lu et interprété par l'ESP32 afin qu'il puisse le convertir en tr/min.

En ce qui concerne le reste de l'électronique, des schémas permettent une compréhension plus précise. Je vous invite à visualiser les ANNEXES 1,2 & 3.

### 5.4. Résultats finaux de la programmation

La programmation est un domaine à part, différent de l'électronique et de la mécanique. Pour cette raison, je ne vais pas expliquer en détail le code utilisé, car il a déjà été brièvement présenté dans la section 2.4 de ce rapport. Cependant, pour une meilleure compréhension, j'ai mis le code à disposition dans le dépôt GitHub que j'ai mentionné dans la section 5.1 de ce rapport.

### 6. CONCLUSION

En conclusion, la conception et la réalisation de cet
aspirateur | numérique | ont | été | une | expérience
enrichissante pour moi en tant qu'étudiant en ingénierie. Malgré un budget limité, j'ai réussi à concevoir et à construire un système efficace en faisant des choix judicieux de composants et en utilisant des principes de traitement du signal appropriés, permettant ainsi d'obtenir des résultats satisfaisants en termes de précision et de rapidité.

Des possibilités d'amélioration sont envisageables pour ce système. En particulier, l'intégration de l'IoT permettrait d'améliorer la surveillance et le contrôle à distance de l'aspirateur. Par ailleurs, l'amélioration du PCB peut également être envisagée, car celui-ci n'intègre actuellement que des composants DIP et des modules éducatifs ou de prototypage tels que le DHT11, le ST7735, le VL6180X, etc. Cette configuration entraîne une consommation d'énergie inutile et est gourmande en espace. Pour remédier à cela, il serait judicieux de concevoir un PCB plus compact avec des composants SMD, sans modules éducatif ou de prototypage, consommant ainsi moins d'énergie.

En somme, je considère que ce projet a été une réussite. Cette étude m'a permis de concevoir un produit fonctionnel et utile. Il représente également une base solide pour d'autres projets similaires à l'avenir.

### 7. RÉFÉRENCES

[1] AntheDesign, Phénomène GoPro & YouTube, https://www.anthedesign.fr/autour-du-web/phenomene-gopro-you-tube/, (https://www.anthedesign.fr/autour-du-web/phenomene-gopro-you-tube/) consulté le 03 mai 2023.
[2] ICRFQ, | 2022, | ESP32 | vs | STM32,
https://www.icrfq.net/esp32vs-stm32/, consulté le 03 mai 2023.
[3] SAP, Qu’est-ce que l’IoT (Internet des objets)?, https://www.sap.com/france/products/artificial-intelligence/what-is-iot-internet-of-things.html, (https://www.sap.com/france/products/artificial-intelligence/what-is-iot-internet-of-things.html) consulté le 03 mai 2023.

## ANNEXES

Annexe 1 : Schéma électronique 1/3 - Microcontrôleur & alimentations

Annexe 2 : Schéma électronique 2/3 - Ventilateur & Traitement du signal

Annexe 3 : Schéma électronique 3/3 - Connecteurs & autres périphériques

Annexe 4 : Rendu 3D - Vue de gauche & de droite

Annexe 5 : Mode d’emploi 1/3 - Prérequis

Annexe 6 : Mode d’emploi 2/3 – Schéma bloc du fonctionnement de l’aspirateur

Annexe 7 : Mode d’emploi 3/3 – Pinouts de l’ESP32

## ANNEXE 1 : SCHEMA ELECTRONIQUE 1/3 - MICROCONTROLEUR & ALIMENTATIONS

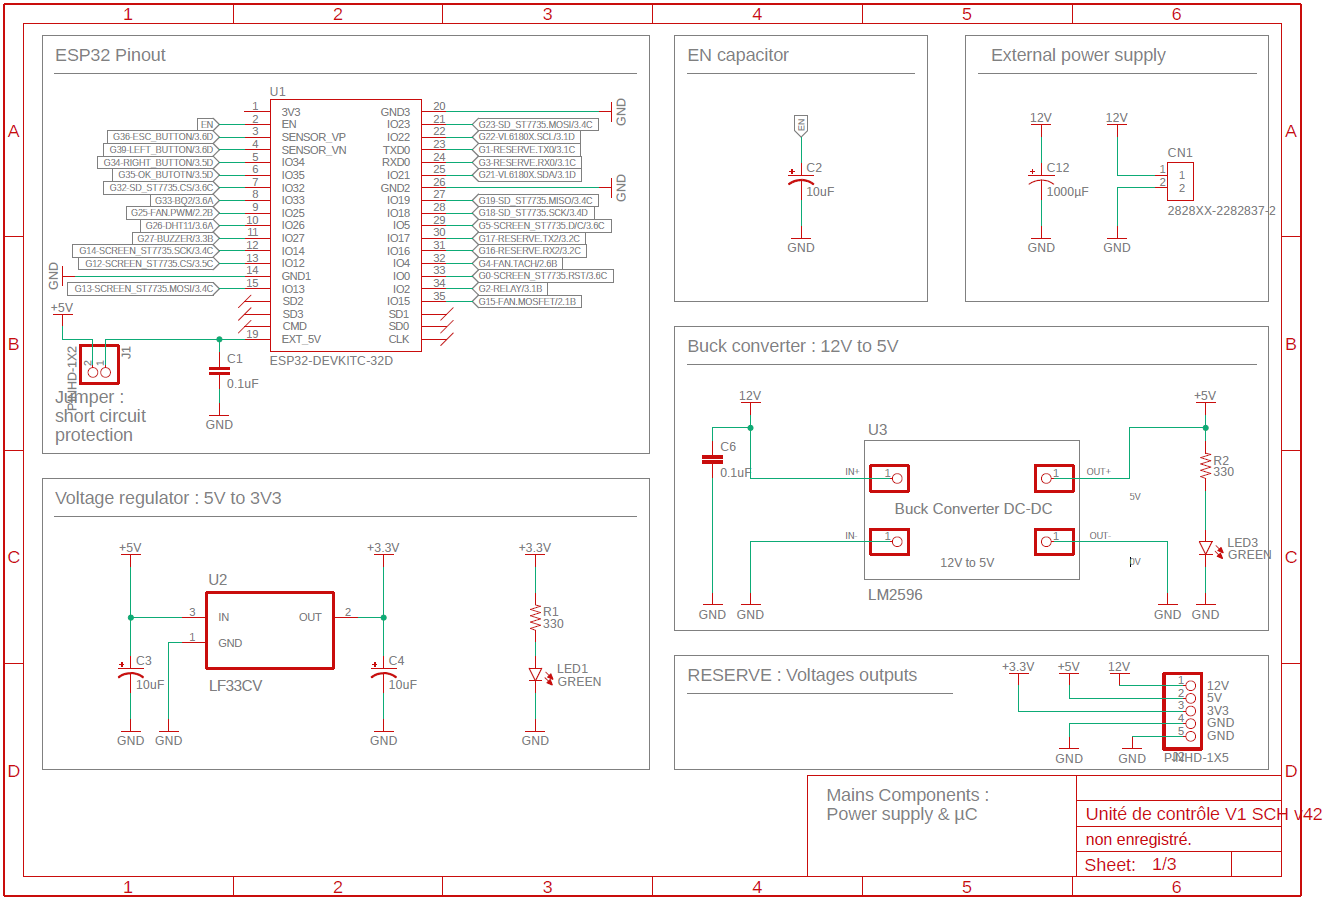
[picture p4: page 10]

## ANNEXE 2 : SCHEMA ELECTRONIQUE 2/3 - VENTILATEUR & TRAITEMENT DU SIGNAL

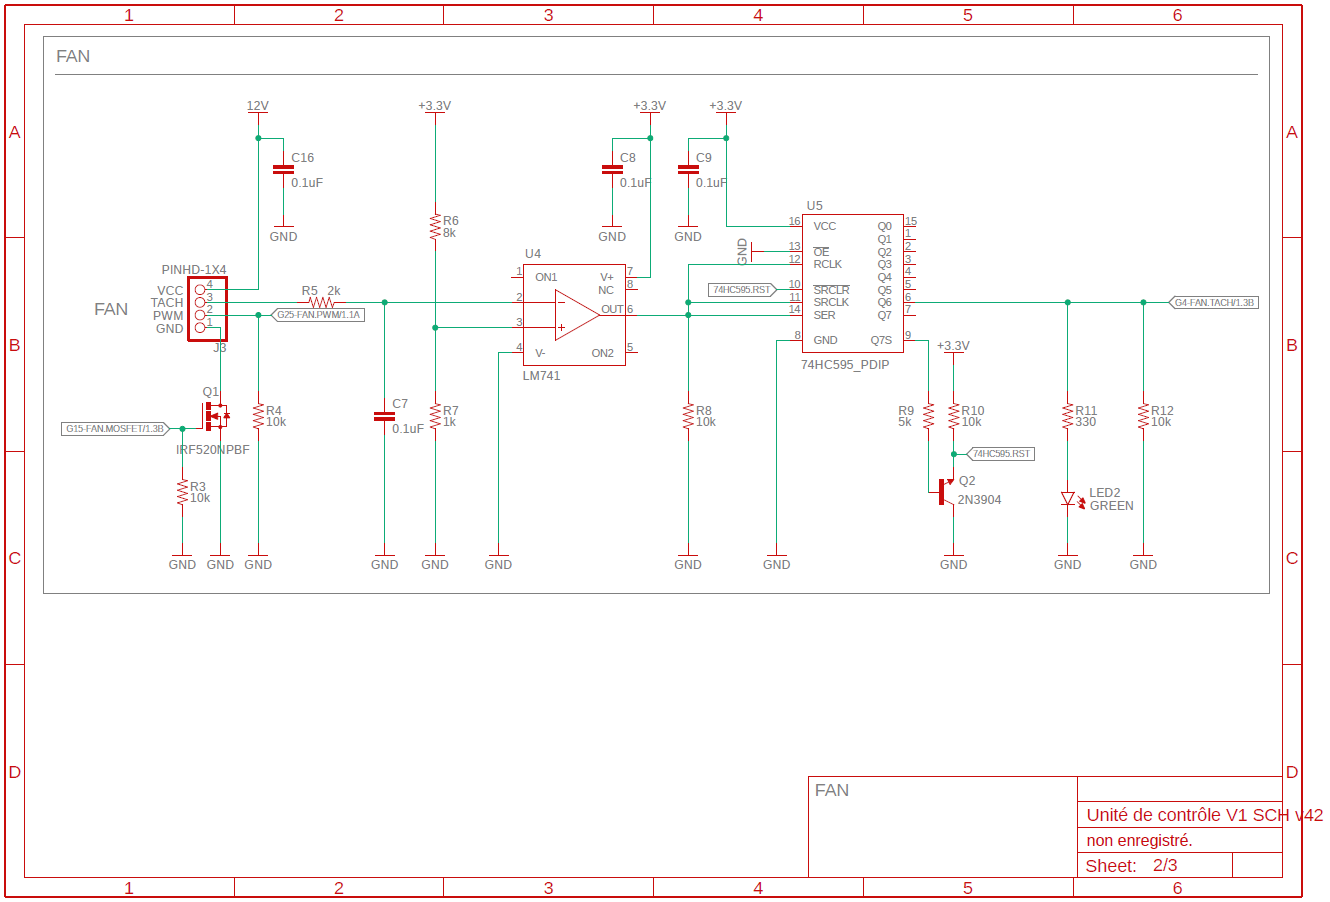
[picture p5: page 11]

## ANNEXE 3 : SCHEMA ELECTRONIQUE 3/3 - CONNECTEURS & AUTRES PERIPHERIQUES

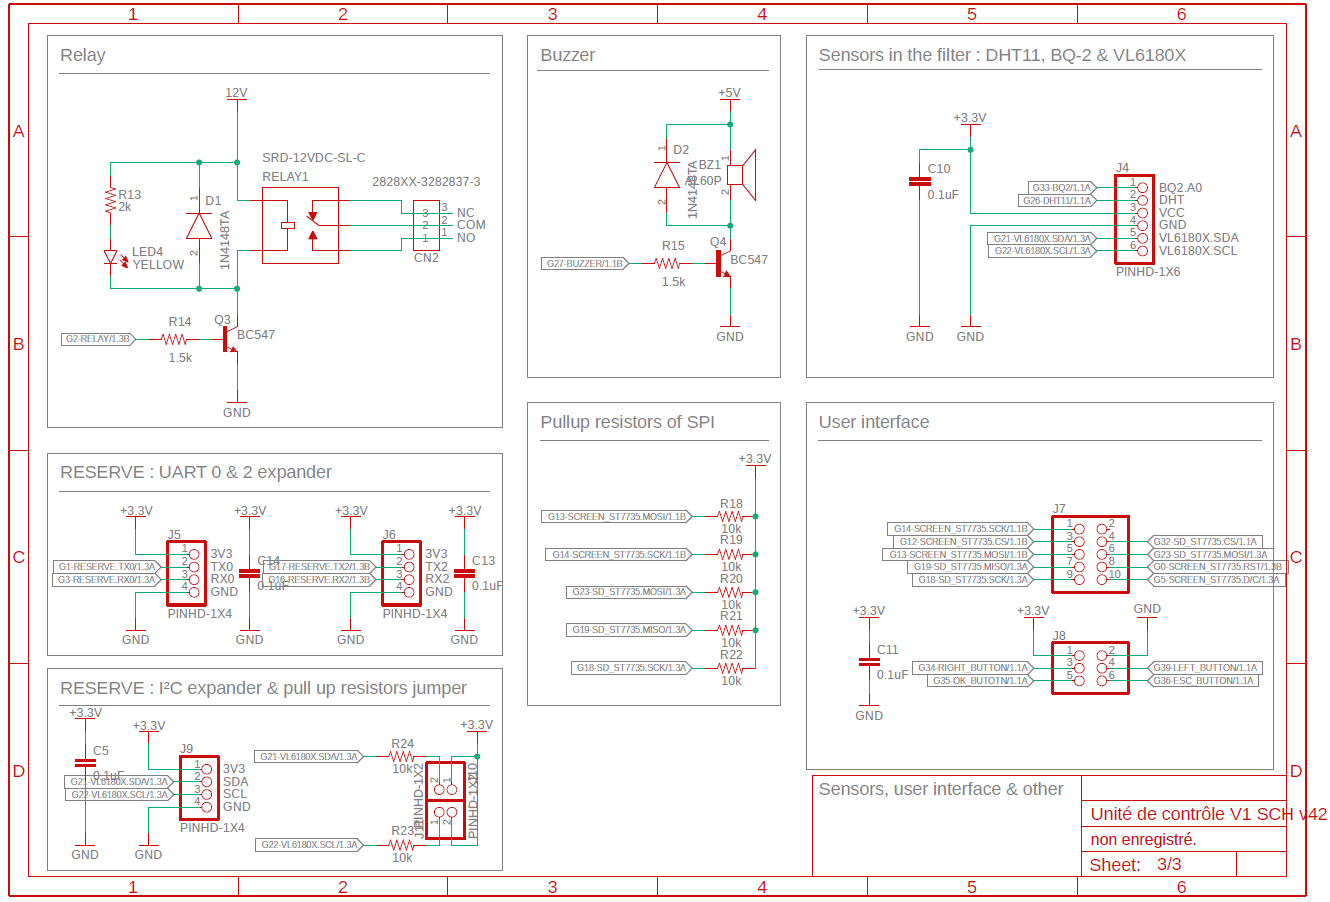
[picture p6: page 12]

## ANNEXE 4 : RENDU 3D - VUE DE GAUCHE & DE DROITE

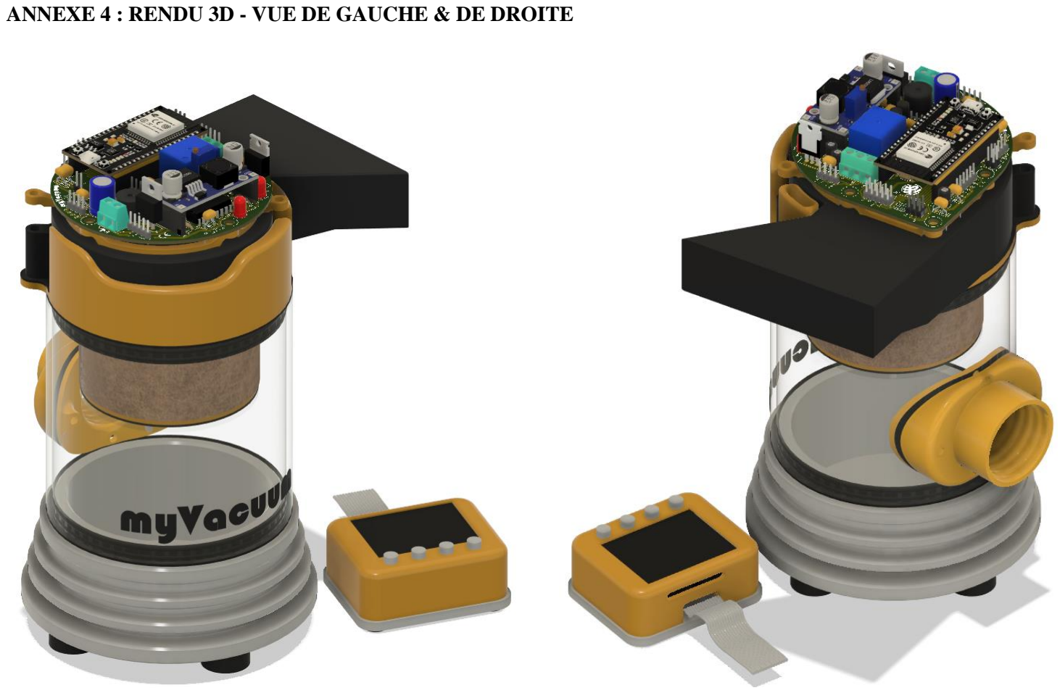
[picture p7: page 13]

Ce manuel d'utilisation a pour but de vous guider tout au long de vos premières manipulations de l'aspirateur, afin que vous puissiez le prendre en main en toute facilité.

### 1. MATERIEL REQUIS

L'alimentation externe n'est pas fournie avec l'aspirateur. Il est donc nécessaire de se procurer une alimentation adaptée à l'appareil, à savoir une alimentation de 12VDC puissant pomper au minimum 5A. La qualité du 12V de l'alimentation peut être tolérée dans une fourchette de 11V à 14V, ce qui signifie qu'une batterie peut également être utilisée.

Une fois que vous disposez d'une alimentation de cette capacité, il vous suffit de connecter le +12V et le 0V aux borniers correspondants de l'aspirateur (1), comme indiqué sur la figure 1. Des indications sont inscrites à côté des borniers pour vous guider et éviter toute confusion.

Par ailleurs, aucune configuration ni logiciel n'est requis pour utiliser l'aspirateur, qui est un produit "plug and play".

### 2. REGLES D’UTILISATION

Lors de la manipulation de l'aspirateur, il est recommandé de saisir l'appareil par sa base en aluminium. En effet, la structure de l'aspirateur est maintenue par un emboîtement par serrage et pourrait se déboîter en cas de manipulation inappropriée.

Il convient de veiller à utiliser l'aspirateur dans des conditions de température optimales. En effet, si la température ambiante dépasse un certain seuil, la dilatation du réservoir pourrait engendrer le détachement des pièces. Une température avoisinant les 20°C, avec une tolérance de +-10°, est recommandée.

Il est important de noter que l'aspirateur n'est pas conçu pour aspirer des liquides, ce qui pourrait entraîner une détérioration prématurée de l'équipement.

De | même, l'utilisation | d'une rallonge de | tube d'aspiration | réduira
considérablement l'efficacité de l'aspirateur en entraînant une perte de charge trop importante. Cette situation mettra en sécurité le ventilateur pour éviter les surcharges.

Il est à noter que l'aspirateur ne possède pas de protection d'inversion de polarité. Il convient donc de ne pas inverser les bornes +12V et 0V en entrée du bornier (1), au risque de subir des conséquences regrettables.

Enfin, il est important de souligner que l'aspirateur n'est pas équipé d'un fusible. Il faudra donc se filler au projet.

### 3. INTERFACE UTILISATEUR

Dans l'annexe 6, vous trouverez un résumé des différentes options proposées par l'interface utilisateur. Pour naviguer entre ces options, vous disposez de 4 boutons : Escape, Left, Right & OK.

Il est important de ne retirer ou d'insérer la carte SD que lorsque l'aspirateur est éteint afin d'éviter tout dysfonctionnement.

### 4. PROGRAMMATION DE L’ESP32 PENDANT LA MISE EN SERVICE

Il est parfaitement envisageable de programmer l'ESP32 (3) durant la mise en service de l'aspirateur. Le PCB intègre une sécurité destinée à éviter les conflits de tensions externes avec celles internes, notamment avec l'USB d'un ordinateur branché, et ainsi éviter les risques de court-circuit.

Pour cela, il suffit de débrancher le cavalier (2) qui interfère avec le connecteur USB de l'ESP32 pour y connecter le câble de programmation. Si ce cavalier n'est pas débranché, il est impossible de connecter le câble de programmation à l’ESP32.

Avant de programmer, je vous recommande de vous référer à l'annexe 7 pour identifier quel périphérique est connecté à quelle broche de l'ESP32.

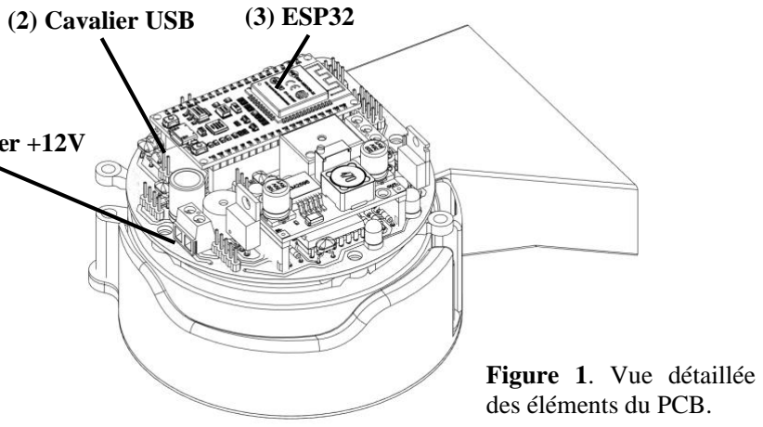
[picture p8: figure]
(2) Cavalier USB; (3) ESP32; Figure 1. Vue détaillée des éléments du PCB.

(1) Bornier +12V

## ANNEXE 5 : MODE D’EMPLOI 1/3 - PREREQUIS

## ANNEXE 6 : MODE D’EMPLOI 2/3 – SCHEMA BLOC DU FONCTIONNEMENT DE L’ASPIRATEUR

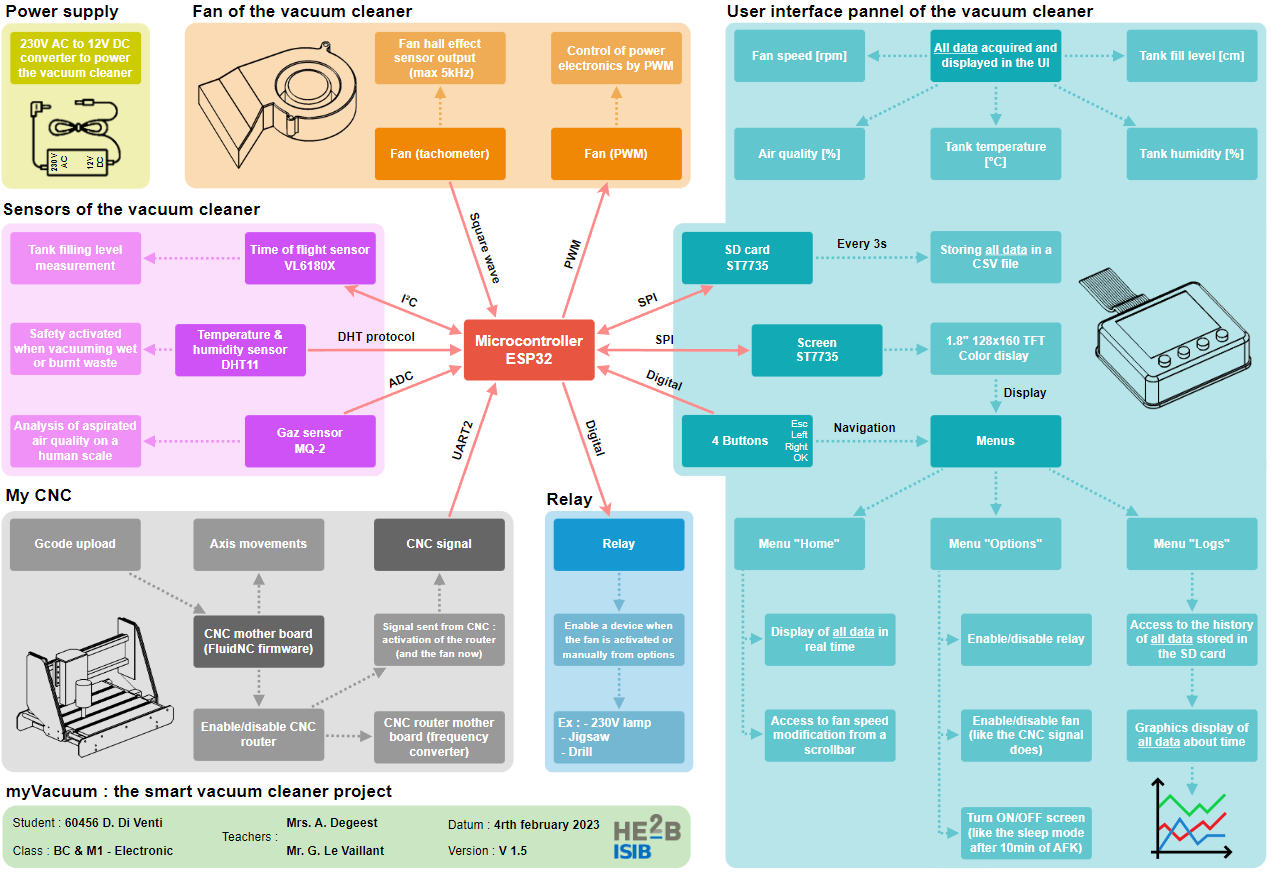
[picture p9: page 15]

## ANNEXE 7 : MODE D’EMPLOI 3/3 – PINOUTS DE L’ESP32

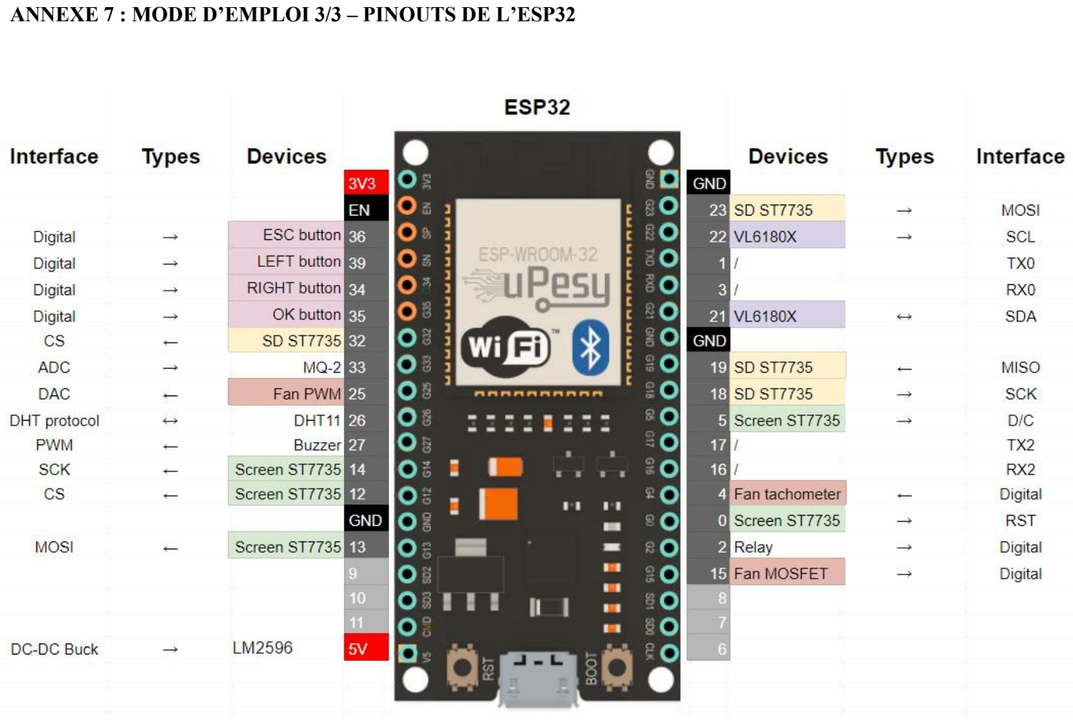
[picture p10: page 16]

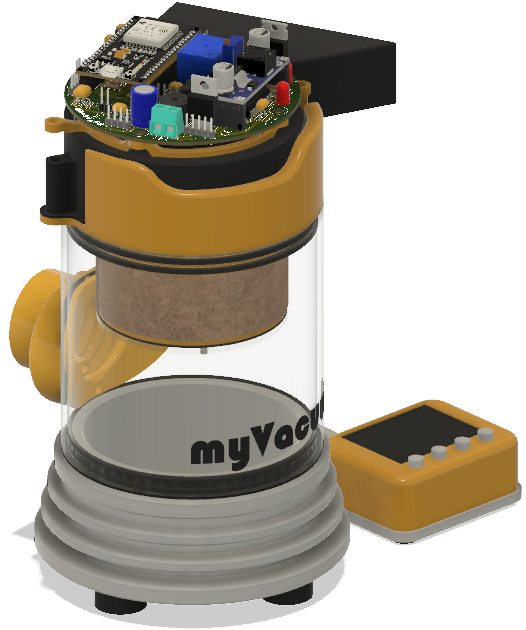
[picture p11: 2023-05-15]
Documents/Images/myVacuum_3D.PNG

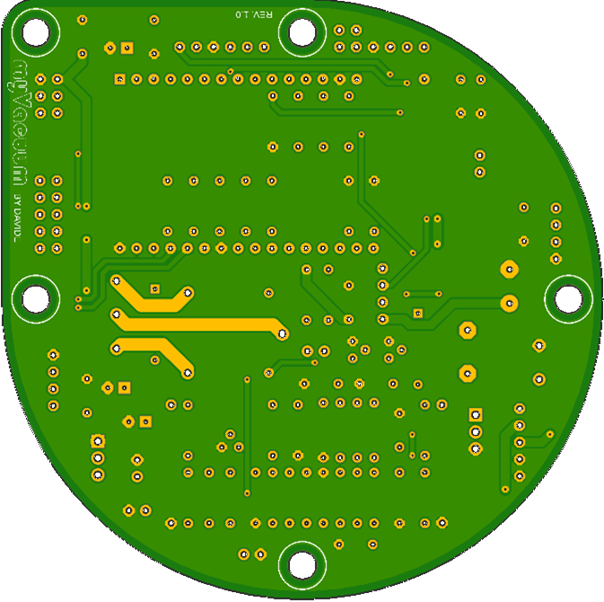
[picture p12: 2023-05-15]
Documents/Images/PCB_Preview_bottom.PNG

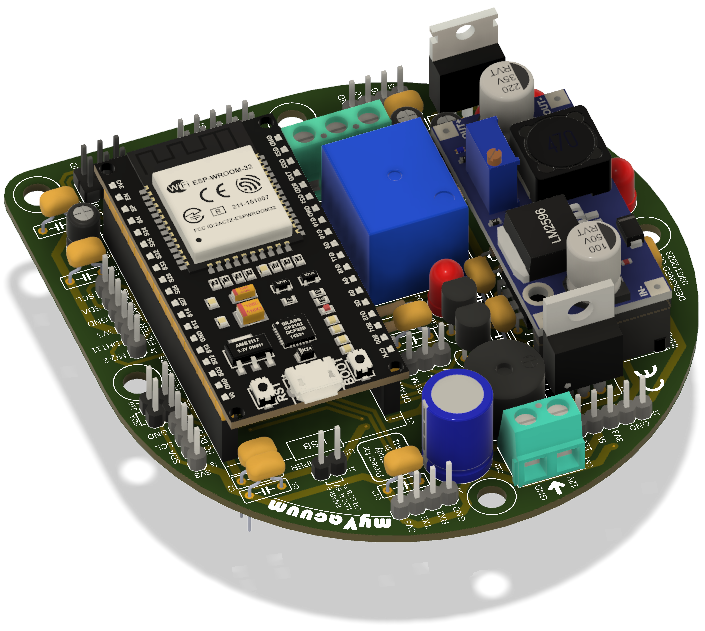
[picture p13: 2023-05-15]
Documents/Images/PCB_3D.PNG

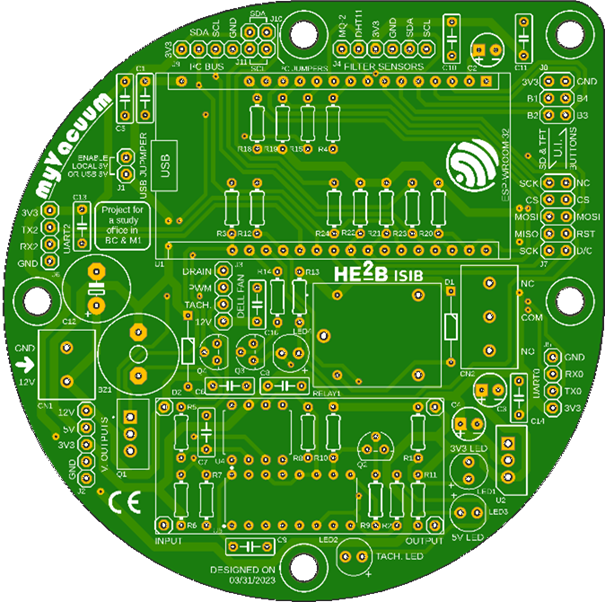
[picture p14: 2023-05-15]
Documents/Images/PCB_Preview_top.PNG

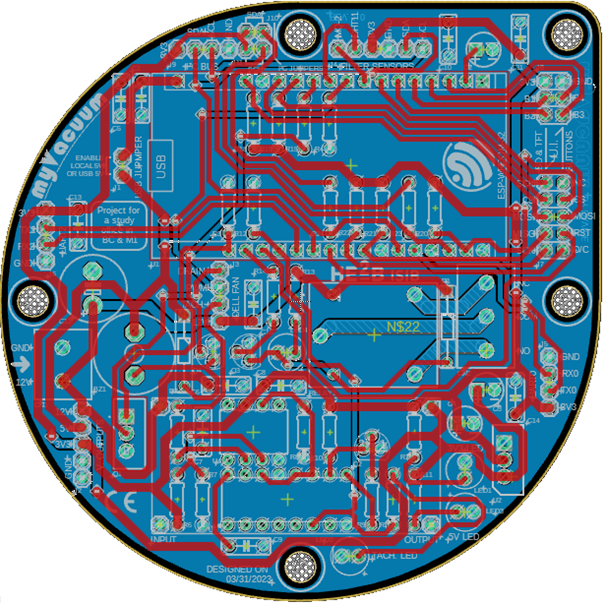
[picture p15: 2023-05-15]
Documents/Images/PCB.png

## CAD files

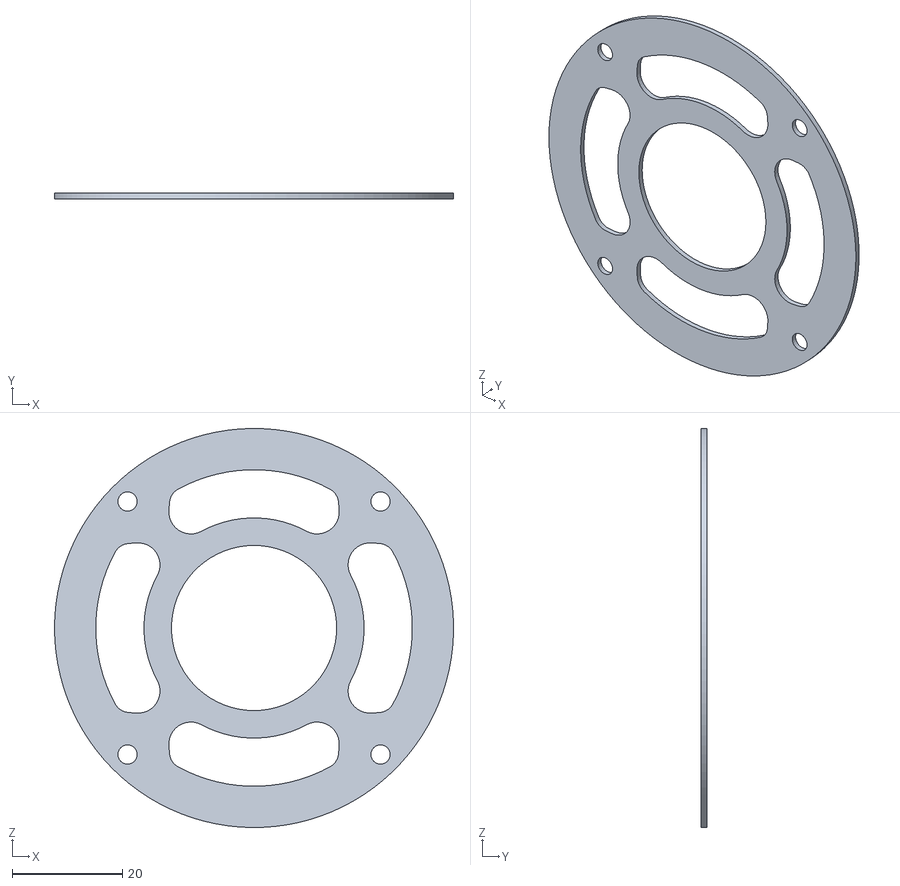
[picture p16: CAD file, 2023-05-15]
Documents/Impressions_3D/TPU-Joint filtre plexiglass.stl
72.5 x 1.00 x 72.5

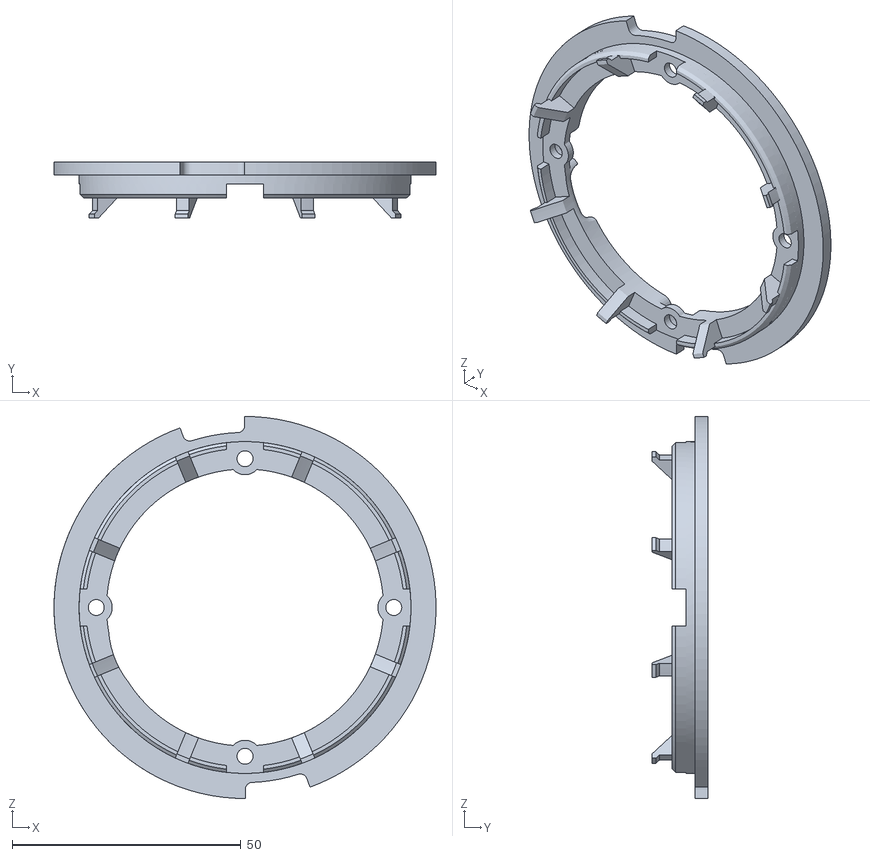
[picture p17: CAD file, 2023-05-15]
Documents/Impressions_3D/PLA-Cage filtre 2.stl
83.5 x 12.2 x 83.5

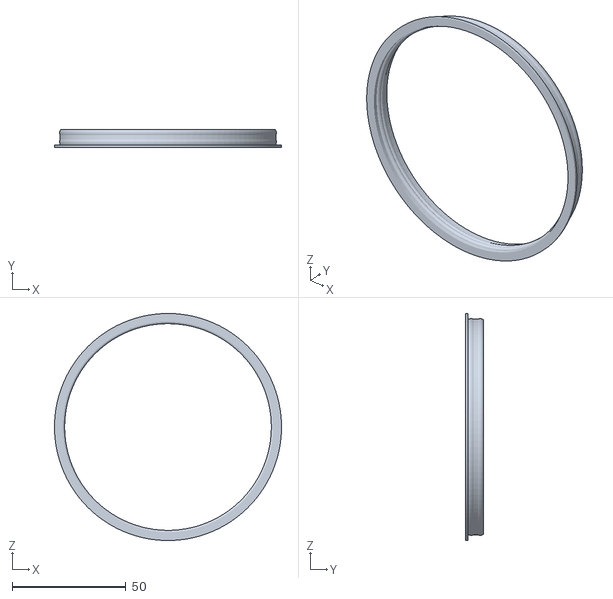
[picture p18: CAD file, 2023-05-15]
Documents/Impressions_3D/TPU-joint réservoir bas.stl
100.0 x 7.90 x 100.0

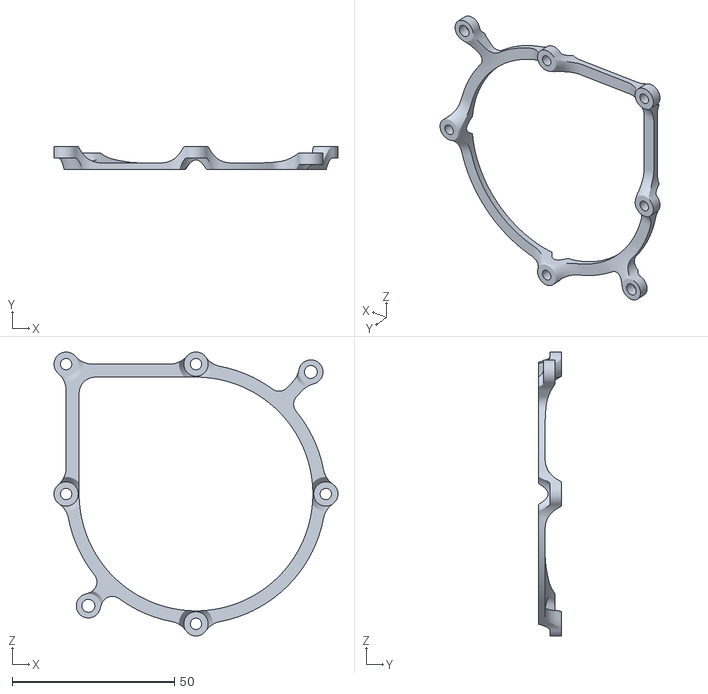
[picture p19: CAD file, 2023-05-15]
Documents/Impressions_3D/PLA-Support PCB.stl
87.5 x 7.00 x 87.5

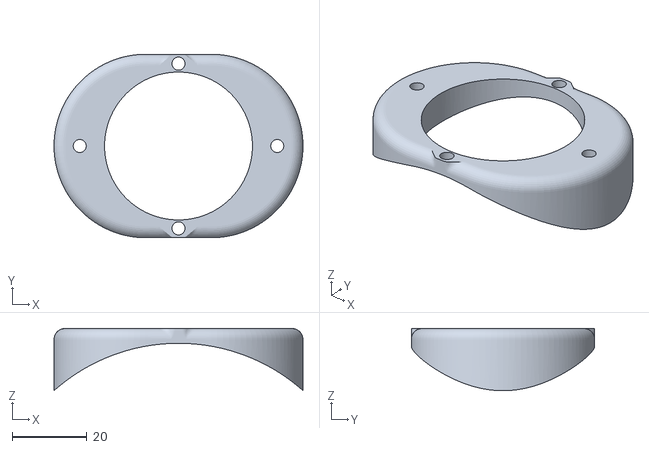
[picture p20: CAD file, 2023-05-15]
Documents/Impressions_3D/PLA-Adaptateur tube aspi 1.stl
66.5 x 49.0 x 16.7

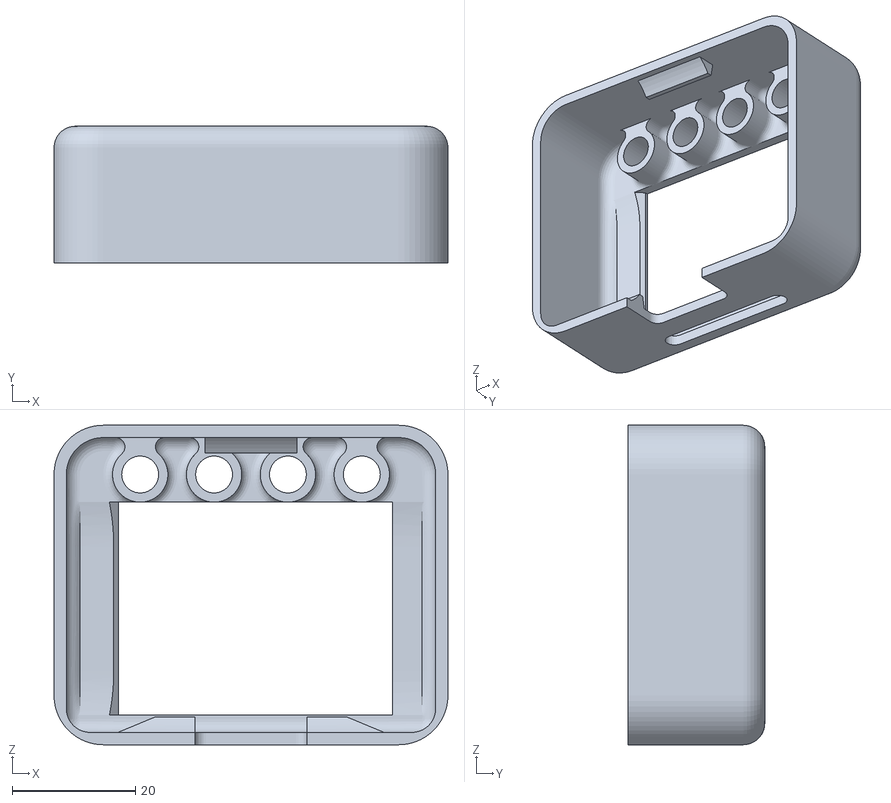
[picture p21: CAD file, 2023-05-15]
Documents/Impressions_3D/PLA-Couvercle (UI).stl
64.0 x 22.2 x 51.9

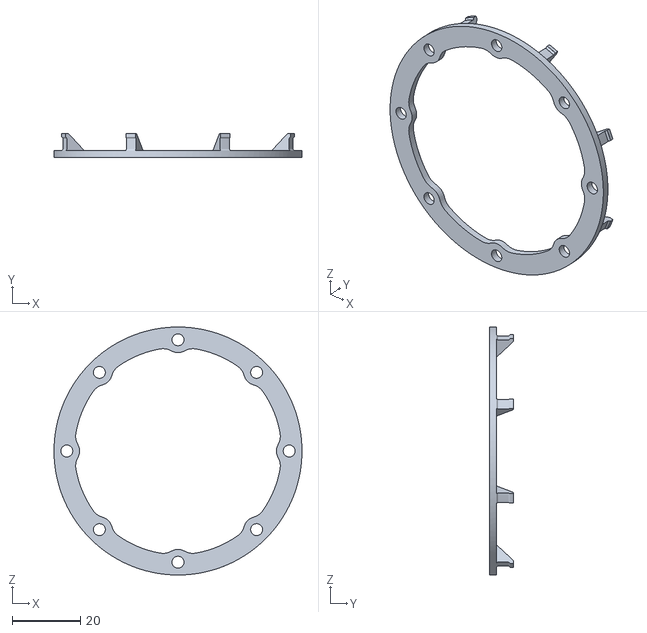
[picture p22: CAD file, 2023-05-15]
Documents/Impressions_3D/PLA-Cage filtre 1.stl
72.5 x 7.00 x 72.5

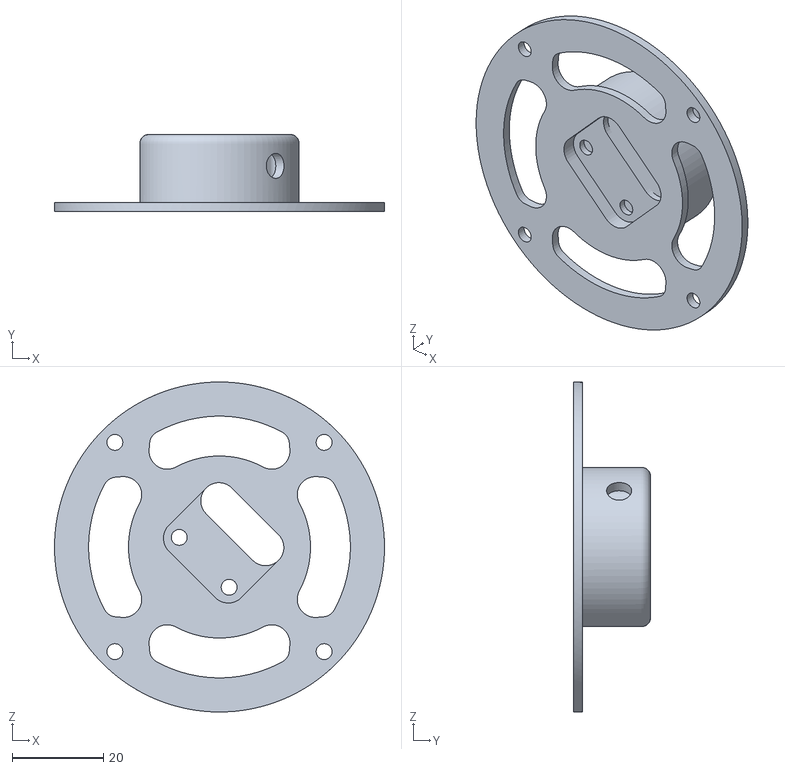
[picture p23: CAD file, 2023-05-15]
Documents/Impressions_3D/PLA-Support capteurs du filtre.stl
72.5 x 17.0 x 72.5

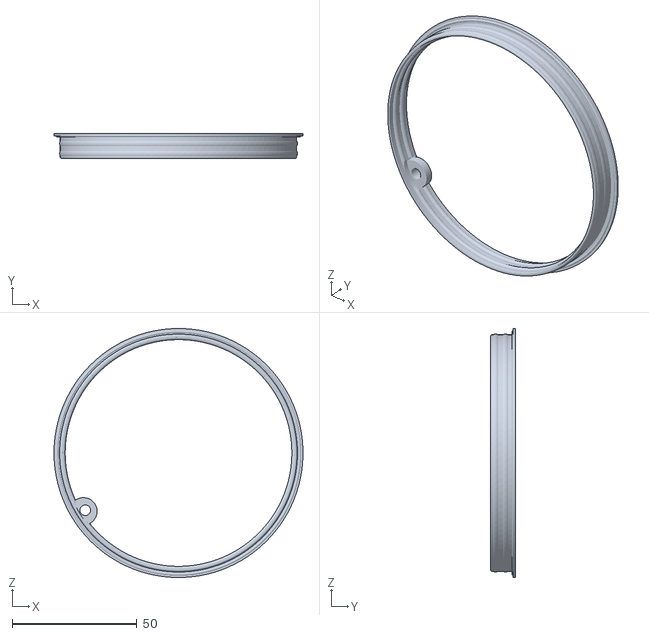
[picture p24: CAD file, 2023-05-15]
Documents/Impressions_3D/TPU-Joint réservoir dessus.stl
100.0 x 10.0 x 100.0

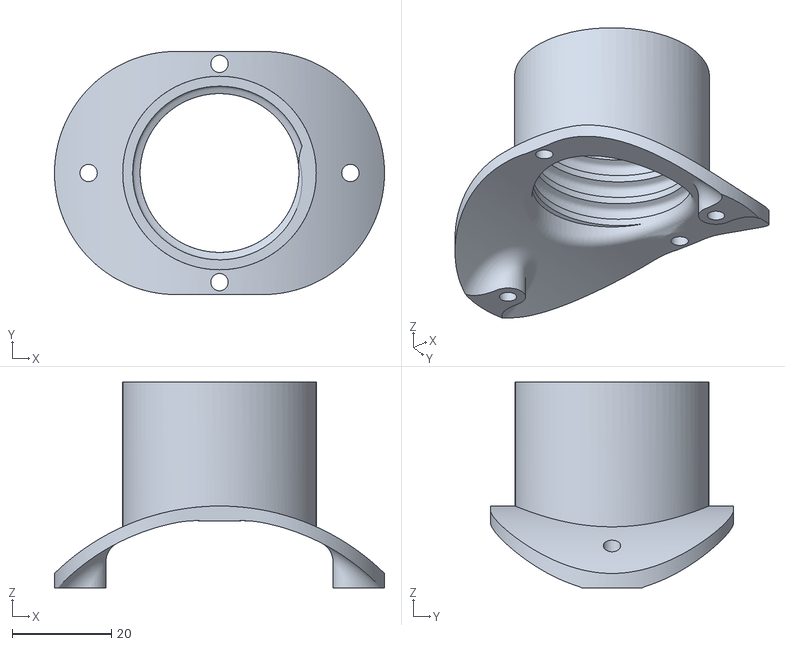
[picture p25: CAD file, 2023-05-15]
Documents/Impressions_3D/PLA-Adaptateur tube aspi 2.stl
66.5 x 49.0 x 41.5

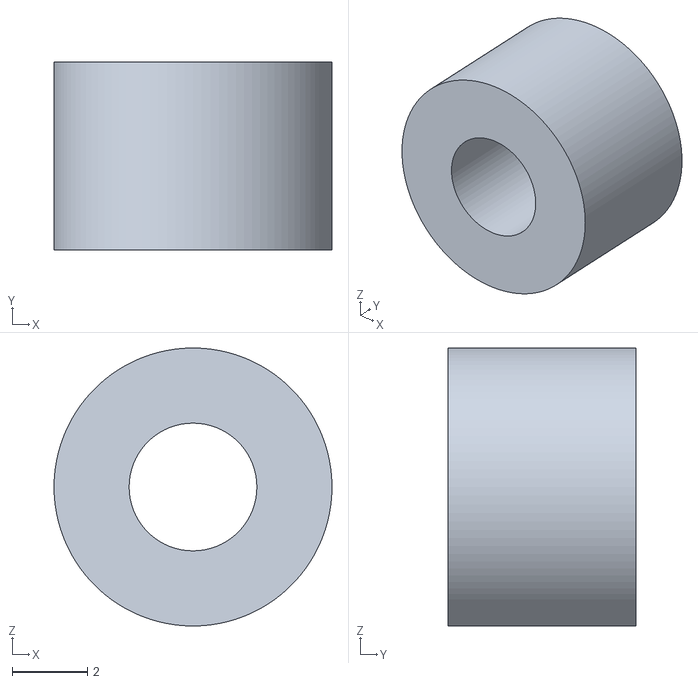
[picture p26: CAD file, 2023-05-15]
Documents/Impressions_3D/PLA-Entretoise M3 4mm (UI).stl
7.40 x 5.00 x 7.40

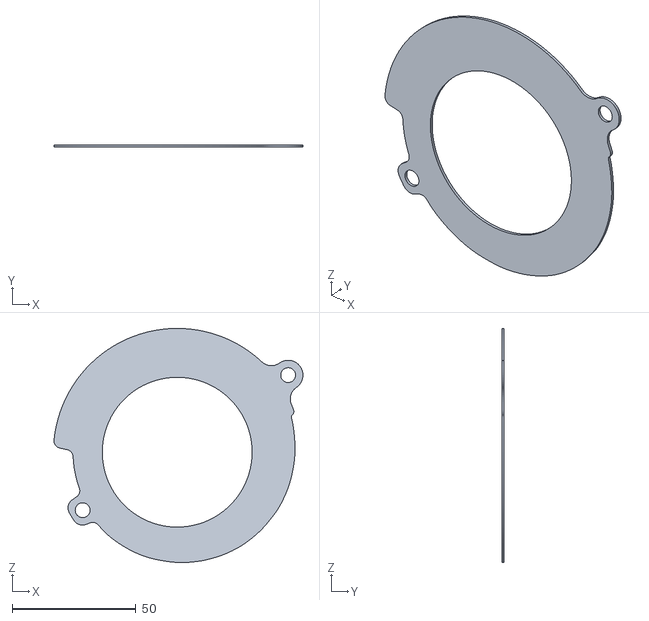
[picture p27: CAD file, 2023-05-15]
Documents/Impressions_3D/TPU-Joint ventilo.stl
100.6 x 1.00 x 94.6

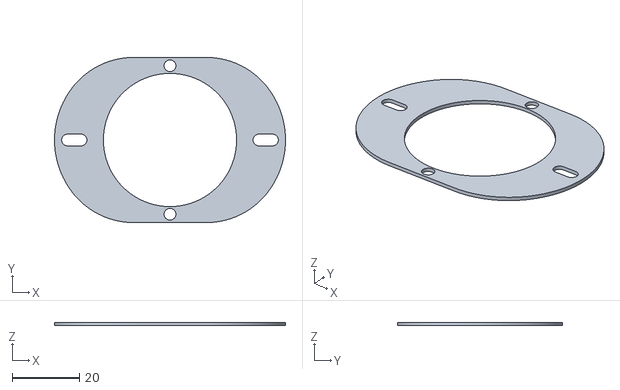
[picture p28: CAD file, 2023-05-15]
Documents/Impressions_3D/TPU-Joint adaptateur tube aspi.stl
68.5 x 49.0 x 1.00

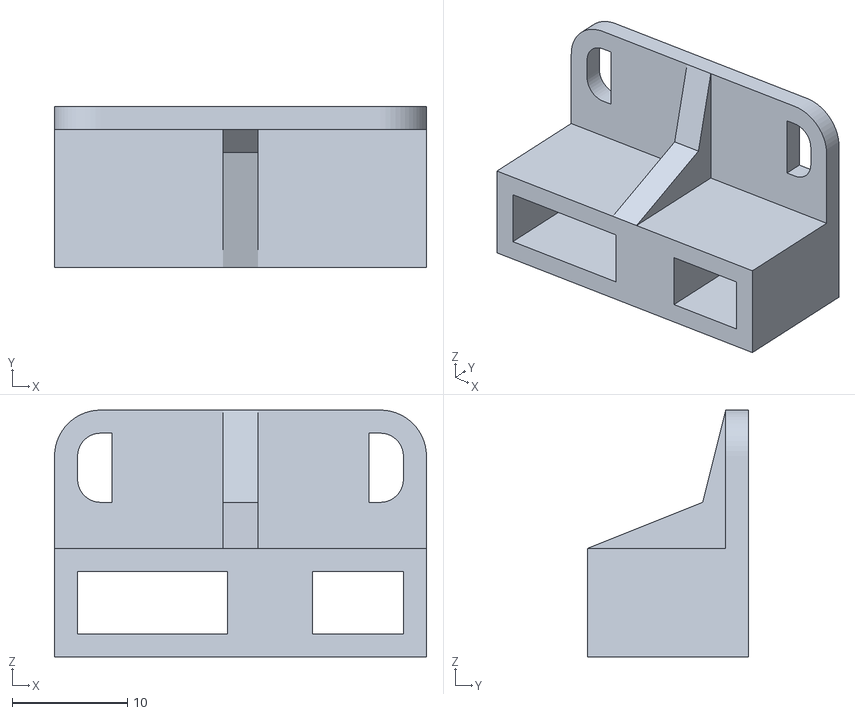
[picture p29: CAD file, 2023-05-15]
Documents/Impressions_3D/PLA-Connecteur UI.stl
32.2 x 14.0 x 21.4

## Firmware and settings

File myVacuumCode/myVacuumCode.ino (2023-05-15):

#include "myClass_DrawOnTheScreen.h" // Adafruit_ST7735 compri
#include "myFunctions_WriteAndReadToSDCard.h"
#include "DHT.h"
#include <Wire.h>
#include "Adafruit_VL6180X.h"

                                     //CS  A0  MOSI  CLK RST
Adafruit_ST7735 tft = Adafruit_ST7735(12, 5, 13,   14, 0);

Adafruit_VL6180X vl = Adafruit_VL6180X();

//Customs Images
int hexFan_width = 32;
int hexFan_height = 32;
String hexFan0 = "1FF800003FFC0000700C0000600600006006000060060000600C0000601C00007038001C3031F87F3837FEE39C7F07C1FE7C03C0FFF803C01FF003C0066003C0066003C00FF803C01FFF03C03E7F83E0FE39C77FEC1CFE3F8C0C38001C0E00003806000030060000600600006006000060060000300E00003FFC00001FF800"; //IDLE
String hexFan1 = "1FFC00003FFF00007001C004600660086006101060020830600C0020601C00607038005C3031F8DB3837FEC39C7F07C1FE7C03C0FFF803C01FF003C0066003C0066003C00FF803C01FFF03C03E7F83E0FE39C37FEC1CDB3F8C0C3A001C0E06003806040030060C10400608086006100660062003800E0000FFFC00003FF800"; //frame 1
String hexFan2 = "7FE00001F0780003C38600070180000E0183F00C008FF80C039E1C0C03380C0C0338062E0370072603E0034781E00343C1C001C1F3C001C07FE7C5BE3E7FDDBBFE7C7DA3E7FE038003CF83800383C2C00781E2C007C064E00EC074601CC030701CC0303879C0301FF100300FC18070000180E00061C3C0001E0F800007FE00"; //frame 2
String hexFan3 = "7C000018FF0000E1C78003C181C0074380E00E6300701C53003838130018701B000C601B007CE01B0024C01F0FC2C00F3E02C00FF800E007FFF078067FFC3FFE601E0FFFE006001FF003407CF00343F0F8032400D8073E00D8063000C80E3800C81C1C00CA380E00C6700701C2E0038183C001E3870000FF1800003E0000"; //frame 3
PixelImage Pixelfan(tft);
int speedometer_width = 15;
int speedometer_height = 15;
String speedometer ="7C03260A0A2002602D0086020E083";
PixelImage Speedometer(tft);

int buttons_width = 32;
int buttons_height = 11;
String backButton0 = "FFFFFFFF8000000180040001800C0001801FF001800C08018004080180000801800FF00180000001FFFFFFFF";
String backButton1 = "3FFFFFFC200000042002000420060004200FE0042006100420021004200010042007E004200000043FFFFFFC";
PixelImage BackButton(tft);
String leftButton0 = "FFFFFFFF80000001800000018008000180180001803FFC0180180001800800018000000180000001FFFFFFFF";
String leftButton1 = "3FFFFFFC200000042000000420040004200C0004201FF804200C00042004000420000004200000043FFFFFFC";
PixelImage LeftButton(tft);
String rightButton0 = "FFFFFFFF80000001800000018000100180001801803FFC0180001801800010018000000180000001FFFFFFFF";
String rightButton1 = "3FFFFFFC20000004200000042000200420003004201FF804200030042000200420000004200000043FFFFFFC";
PixelImage RightButton(tft);
String okButton0 = "FFFFFFFF80000001800E44018011480180115001801160018011500180114801800E440180000001FFFFFFFF";
String okButton1 = "3FFFFFFC2000000420064804200950042009600420094004200960042009500420064804200000043FFFFFFC";
PixelImage OkButton(tft);

int sensors_width = 11;
int sensors_height = 16;
String waterDrop = "40140280881104108220240500600C01404808C6070";
PixelImage WaterDrop(tft);
String thermometer = "E022C4408A11022C540AA150491392FA5F49C8820F8";
PixelImage Thermometer(tft);
String leaf = "E064308822048090244490921284508460B0200400";
PixelImage Leaf(tft);

int runStopButtons_width = 32;
int runStopButtons_height = 11;
String runButton0 = "FFFFFFFF8000000180F22881808A2881808A2C8180F22A8180A22981809228818089C88180000001FFFFFFFF"; //waiting
String runButton1 = "E00000078000000180F22881008A2880008A2C8000F22A8000A22980009228808089C88180000001E0000007";//up
String runButton2 = "3FFFFFFC2000000420722904204A2904204A2D0420722B0420522B04204A29042049C904200000043FFFFFFC"; //click
PixelImage RunButton(tft);
String stopButton0 = "FFFFFFFF80000001839F39E18455451184044511838445E180444501844445018384390180000001FFFFFFFF"; //waiting
String stopButton1 = "E000000780000001839F39E10455451004044510038445E000444500044445008384390180000001E0000007"; //up
String stopButton2 = "3FFFFFFC20000004219F39C42255452422044524218445C4204445042244450421843904200000043FFFFFFC"; //click
PixelImage StopButton(tft);

int speedCursor_width = 12;
int speedCursor_height = 12;
String speedCursor0 = "F03FC7FE7FEFFFFFFFFFFFF7FE7FE3FC0F0";
String speedCursor1 = "0xF030C40240280180180180140240230C0F0";
PixelImage SpeedCursor(tft);
int arrowsCursor_width = 12;
int arrowsCursor_height = 5;
String arrowsCursor0 = "204606FFF606204";
String arrowsCursor1 = "0";
PixelImage ArrowsCursor(tft);

int menuCursor_width = 11;
int menuCursor_height = 7;
String menuCursor0 = "802808820880A00FFF";
String menuCursor1 = "0";
PixelImage MenuCursor(tft);

int optionCursor_width = 8;
int optionCursor_height = 11;
String optionCursor0 = "6050484442414244485060";
String optionCursor1 = "0";
PixelImage OptionCursor(tft);

int speaker_width = 17;
int speaker_height = 14;
String speaker = "C000A0809020888B842502918124C09260523C21211110481014100600";
PixelImage Speaker(tft);
int moon_width = 15;
int moon_height = 15;
String moon = "E0068012004800900220044008803080E082A0FA4004401060C03E0";
PixelImage Moon(tft);
int relayIcon_width = 15;
int relayIcon_height = 7;
String relayIcon = "7FF11FF41FF83FF07FD1FF1FFC";
PixelImage RelayIcon(tft);

long int counter; //compteur permettant aux animations de sélectionner leurs frame à afficher.
int frame; //image actuelle de l'animation en cours

// Variables boutons
const int escapeButton = 34;
const int leftButton = 35;
const int rightButton = 36;
const int okButton = 39;
int escapeButtonValue = 0;
int leftButtonValue = 0;
int rightButtonValue = 0;
int okButtonValue = 0;
int lastEscapeButtonValue = 0;
int lastLeftButtonValue = 0;
int lastRightButtonValue = 0;
int lastOkButtonValue = 0;

// Variables commande fan
const int PWMfanPin = 25;                                         // Pin PWM fan                                      // Précision binaire de la modulation de largeur d'impultion
const int fanMOSFET = 15;                                         // Pin relais

// Variables lecture fan [tr/min]
const int PinTachymetre = 4;                                      // PIN du tachymetre
volatile byte tours = 0;                                          // Nombre de tours comptés
unsigned long tempsPrecedent = 0;                                 // Temps du dernier tour
unsigned long temps = 0;                                          // Temps total écoulé depuis le démarrage
const int delai = 1800;                                           // Durée en millisecondes pour calculer les tours par minute (lecture toutes les "delai" ms) (0-10000RPM)
int toursParMinute = 0;

//Flags d'affichage fréquentiels
int myDislplayClock;                                              // Fréquence d'affichage/d'actualisation des données à afficher dans l'écran (toutes les 300ms)
int flagMyDislplayClock;                                          // Front montant de cette fréquence
int myOldDislplayClock;                                           // Front déscandant de cette fréquence

//Quelques capteurs et valeurs...
uint8_t tankFillLevel;          //niveau de remplissage du réservoir (0-71mm)
int maxTankFillLevel = 71;      //hauteur maximum que peuvent atteindre les déchets
#define DHTPIN 26
#define DHTTYPE DHT11
DHT dht(DHTPIN, DHTTYPE);
int pinRelay = 2;
int pinMQ2 = 33;
int pinBuzzer = 27;
int humidity;                   //humidité (0-100%)
int temperature;                //température (0-50°C)
int airQuality;                 //Qualité d'air (0-4095)->(0-2048 = 0-100%)

//Flags des menus
int menuSetup = 0;                //flag mis à 1 une fois que le setup (affichages de widget) d'un menu est executé
int menuSelection;                // 0: DASHBOARD ; 1:LOGS ; 2: OPTION
int previousMenuSelection;        //...
int isInMenu;                     //flag permettant de savoir si l'opérateur est rentré dans un menu (dès qu'il a cliqué sur OK)
int okCount;                      //permet d'identifier à quel endroit nous sommes en ayant cliqué une ou plus de fois (sous-menu, sous-sous menu, ...)
int indexSelection;               //permet d'identifier à quel endroit nous sommes en ayant cliqué une ou plus de fois (sous-menu, sous-sous menu, ...) suite à okCount
int previousOkCount;              //...
int dacValueIsEnable;             //permet de savoir l'instant où on souhaite varier la vitesse (appui sur slider) afin de de lancer le DAC
int dacValue = 190;               //le slider sera à 50% au démarrage
int isRunning = 0;                //Flag permettant de savoir si le ventilateur tourne ou pas
int buzzerEnabled = 1;            //OPTION : flag permettant la sonorisation aprrès du buzzer. Si 1 il y a bip, si 0 (donc modifié depuis les OPTION) alors plus de bip
int relayEnabled = 0;             //OPTION : falg permettant d'allumer ou éteindre le relai depuis les OPTIONS
int afkModeEnabled = 0;           //OPTION : flag permettant d'activer ou non la mise en veille du système depuis les OPTIONS
int disableAFKCountdown = 1;      //OPTION : flag permettant de désactiver ou pas la mise en veille du système après 10min de mise en service de l'aspirateur
int previousAfkModeEnabled = 0;   //Après mise en veille, il ne faut plus répeter qu'il faut mettre en veille car il est déjà en veille, donc cette variable gère les front montant de ce procédé

//Liste des signaux affichés dans les LOGS
#define LIST_LENGTH 102                               //Liste de 100 données utiles lue toutes les 300ms
int logsValues_VL[LIST_LENGTH] = {-1};                //Liste des données du capteur de niveau de remplissage (par défaut rempli à -1, cela permet de ne pas confondre avec un 0 qui pourrait etre mesuré) (-1 pour dire que la l'emplacement de cette donnée est vide)
int previousLogsValues_VL[LIST_LENGTH] = {-1};        //Liste des données précédentes. Cela permet d'effacer les anciennes données pour laisser place aux nouvelles.
int logsValues_MQ2[LIST_LENGTH] = {-1};               //...Capteur de qualité d'air
int previousLogsValues_MQ2[LIST_LENGTH] = {-1};       //...
int logsValues_TACH[LIST_LENGTH] = {-1};              //...Capteur de vitesse
int previousLogsValues_TACH[LIST_LENGTH] = {-1};      //...
int logsValues_DHT_HUM[LIST_LENGTH] = {-1};           //...Capteur d'humidité
int previousLogsValues_DHT_HUM[LIST_LENGTH] = {-1};   //...
int logsValues_DHT_TEMP[LIST_LENGTH] = {-1};          //...Capteur de température
int previousLogsValues_DHT_TEMP[LIST_LENGTH] = {-1};  //...

void shiftLogsValues(int listValues[LIST_LENGTH]) {
  /* Permet de décaller les valeurs d'une liste vers la gauche d'une position.
   * Utilisé pour gerer l'affichage des pixels des courbes du menu LOGS
   */
  for (int i = 0; i < LIST_LENGTH-1; i++) {           // Décalage des valeurs d'une position vers la gauche
    listValues[i] = listValues[i+1];
  }
  listValues[LIST_LENGTH-1] = -1;                   
}

void allMinOneLogsValues(int listValues[LIST_LENGTH]) {
  /* Initialise les listes avec 102 fois -1 à chaque position. 
   * Permet de ne pas afficher de pixel inutiles si le menu LOGS a été ouvert pour la première fois.
   * Cela revient à ce que les courbes évolue dans le temps de droite vers gauche, sans qu'il y ai des signaux inutiles avant.
   */
  for (int i = 0; i < LIST_LENGTH-1; i++) { 
    listValues[i] = -1;
  }
  listValues[LIST_LENGTH-1] = -1; 
}
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
void loop() {
  /* Lit les valeurs des boutons physique de l'inteface utilisateur.
   * Gère les flag pour la getion des menu en fonction des appuis sur boutons
   * Calcule le valeurs des capteurs toutes les 300ms:
   *    Vitesse du ventilateur (RPM - toutes les 1800ms)
   *    Niveau de remplissage du réservoir (mm)
   *    Humidité (%)
   *    Température (°C)
   *    Qualité d'air (%)
   * Gère l'activation de la mise en veille du système entier
   */

  escapeButtonValue = digitalRead(escapeButton);
  leftButtonValue = digitalRead(leftButton);
  rightButtonValue = digitalRead(rightButton);
  okButtonValue = digitalRead(okButton);
      
  if (escapeButtonValue == 1 && lastEscapeButtonValue == 0){                                                    
     BackButton.drawFrame(0, 116, 1, ST7735_WHITE);   
     dacValueIsEnable = 0;
     indexSelection =0;
     okCount = 0;
     if(buzzerEnabled) buzzer();
     if(afkModeEnabled) ESP.restart();
     
   }
   else if (escapeButtonValue == 0 && lastEscapeButtonValue == 1 and not afkModeEnabled) {                                      
     BackButton.drawFrame(0, 116, 0, ST7735_WHITE); 
     
   }
   
   if (leftButtonValue == 1 && lastLeftButtonValue == 0){                                                  
     LeftButton.drawFrame(42, 116, 1, ST7735_WHITE);   
     if(menuSelection>0 and okCount == 0) menuSelection--;
     if(indexSelection>0 and isInMenu and not dacValueIsEnable) indexSelection--;
     if(buzzerEnabled) buzzer();
     if(afkModeEnabled) ESP.restart();
   }
   else if (leftButtonValue == 0 && lastLeftButtonValue == 1 and not afkModeEnabled) {       
     LeftButton.drawFrame(42, 116, 0, ST7735_WHITE);    
   }
   if (leftButtonValue == 1){                                               
     if (dacValue < 200 and dacValueIsEnable and flagMyDislplayClock)dacValue+=1; 
   }
   
   if (rightButtonValue == 1 && lastRightButtonValue == 0){                                                  
     RightButton.drawFrame(84, 116, 1, ST7735_WHITE); 
     if(menuSelection<2 and okCount == 0) menuSelection++;  
     if(isInMenu and not dacValueIsEnable) indexSelection++;
     if(buzzerEnabled) buzzer();
     if(afkModeEnabled) ESP.restart();
   }
   else if (rightButtonValue == 0 && lastRightButtonValue == 1 and not afkModeEnabled) {       
     RightButton.drawFrame(84, 116, 0,ST7735_WHITE);    
   }
   if (rightButtonValue == 1 ){                                                      
     if (dacValue > 180 and dacValueIsEnable and flagMyDislplayClock)dacValue-=1;       
   }
   
   if (okButtonValue == 1 && lastOkButtonValue == 0){                                                  
     OkButton.drawFrame(126, 116, 1, ST7735_WHITE);   
     okCount++; 
     if(buzzerEnabled) buzzer();
     if(afkModeEnabled) ESP.restart();
   }
   else if (okButtonValue == 0 && lastOkButtonValue == 1 and not afkModeEnabled) {       
     OkButton.drawFrame(126, 116, 0, ST7735_WHITE);    
   }

   if (afkModeEnabled == 0){
     if (isRunning){
       temps = micros() - tempsPrecedent;                                               // Calcul du temps écoulé depuis le dernier tour
       if (temps >= delai * 1000) {                                                     // Si le temps écoulé est supérieur à la durée choisie (toutes les "delai" milisecondes il va prendre le nombre de tours effectués dans ce laps de temps pour calculer les rpm)
         detachInterrupt(digitalPinToInterrupt(PinTachymetre));                         // Désactivation de l'interruption pour éviter les compteurs parallèles
         toursParMinute = ((tours * 60 / (temps / 1000000.0))/2)*8;                   // Calcul des tours par minute (/2 car il y a 2 pole par tour dans l'axe du ventilateur)(*8 car le registre divise par 8 la vraie fréquence)
         tours = 0;                                                                     // Réinitialisation du nombre de tours
         tempsPrecedent = micros();                                                     // Mise à jour du temps pour le prochain calcul
         attachInterrupt(digitalPinToInterrupt(PinTachymetre), compterTours, RISING);   // Réactivation de l'interruption pour compter les tours suivants
       }
     }
     myDislplayClock = (millis()/300)%2;
     if (myDislplayClock == 1 and myOldDislplayClock == 0){
       flagMyDislplayClock = 1;
       counter++; 
       uint8_t range = vl.readRange();
       uint8_t status = vl.readRangeStatus(); 
       tankFillLevel = range;
       airQuality = analogRead(pinMQ2);
       humidity = dht.readHumidity();
       temperature = dht.readTemperature();
       if (isnan(humidity) || isnan(temperature)) {
          temperature = 0;
          humidity = 0;
       }
       
        if (previousMenuSelection != menuSelection){ //changement de menu
          tft.fillRect(1,16,156,94, 0x0000); //on efface le contenu des anciennes fenetres
          //Dashboard
          tft.drawLine(0,1,0,15, 0x0000); //x,y à x,y
          tft.drawLine(0,1,67,1, 0x0000);
          tft.drawLine(67,1,67,15, 0x0000);
          tft.drawLine(67,15,157,15, 0x0000);
          //logs
          tft.drawLine(67,15,0,15, 0x0000); 
          tft.drawLine(67,1,67,15, 0x0000);
          tft.drawLine(67,1,104,1, 0x0000);
          tft.drawLine(104,1,104,15, 0x0000);
          tft.drawLine(104,15,157,15, 0x0000);    
          //Options
          tft.drawLine(104,15,0,15, 0x0000); 
          tft.drawLine(104,1,157,1, 0x0000); 
          tft.drawLine(104,1,104,15, 0x0000);
          tft.drawLine(157,1,157,15, 0x0000);
          menuSetup =0;
       }
       if (menuSelection == 0 ){
             
          menuDashboard(); 
       }
       else if (menuSelection == 1){     
       
          menuLogs();
       }
       else if (menuSelection == 2 ){     
          
          menuOptions();
       }
  
       previousMenuSelection = menuSelection;     
     }
     else {
      flagMyDislplayClock = 0;
     }

     if (millis() > 600000 and not isRunning and disableAFKCountdown){
      afkModeEnabled = 1;
      digitalWrite(fanMOSFET, LOW);
     }
   }
   lastEscapeButtonValue = escapeButtonValue;
   lastLeftButtonValue = leftButtonValue;
   lastRightButtonValue = rightButtonValue;
   lastOkButtonValue = okButtonValue;
   myOldDislplayClock = myDislplayClock;
  
   if (afkModeEnabled == 1 and previousAfkModeEnabled ==0){
     tft.fillScreen(ST77XX_BLACK);
     detachInterrupt(digitalPinToInterrupt(PinTachymetre));
     delay(200);
     for(int i = 0; i < 3; i++){
       digitalWrite(pinBuzzer, HIGH);
       delay(50);
       digitalWrite(pinBuzzer, LOW);
       delay(50);       
     }
   }
   previousAfkModeEnabled = afkModeEnabled;
   
}

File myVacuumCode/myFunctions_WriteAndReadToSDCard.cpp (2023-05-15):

#include "myFunctions_WriteAndReadToSDCard.h"

//SD

void listDir(fs::FS &fs, const char * dirname, uint8_t levels){
  Serial.printf("Listing directory: %s\n", dirname);

  File root = fs.open(dirname);
  if(!root){
    Serial.println("Failed to open directory");
    return;
  }
  if(!root.isDirectory()){
    Serial.println("Not a directory");
    return;
  }

  File file = root.openNextFile();
  while(file){
    if(file.isDirectory()){
      Serial.print("  DIR : ");
      Serial.println(file.name());
      if(levels){
        listDir(fs, file.name(), levels -1);
      }
    } else {
      Serial.print("  FILE: ");
      Serial.print(file.name());
      Serial.print("  SIZE: ");
      Serial.println(file.size());
    }
    file = root.openNextFile();
  }
}

void createDir(fs::FS &fs, const char * path){
  Serial.printf("Creating Dir: %s\n", path);
  if(fs.mkdir(path)){
    Serial.println("Dir created");
  } else {
    Serial.println("mkdir failed");
  }
}

void removeDir(fs::FS &fs, const char * path){
  Serial.printf("Removing Dir: %s\n", path);
  if(fs.rmdir(path)){
    Serial.println("Dir removed");
  } else {
    Serial.println("rmdir failed");
  }
}

void readFile(fs::FS &fs, const char * path){
  Serial.printf("Reading file: %s\n", path);

  File file = fs.open(path);
  if(!file){
    Serial.println("Failed to open file for reading");
    return;
  }

  Serial.print("Read from file: ");
  while(file.available()){
    Serial.write(file.read());
  }
  file.close();
}

void writeFile(fs::FS &fs, const char * path, const char * message){
  Serial.printf("Writing file: %s\n", path);

  File file = fs.open(path, FILE_WRITE);
  if(!file){
    Serial.println("Failed to open file for writing");
    return;
  }
  if(file.print(message)){
    Serial.println("File written");
  } else {
    Serial.println("Write failed");
  }
  file.close();
}

void appendFile(fs::FS &fs, const char * path, const char * message){
  Serial.printf("Appending to file: %s\n", path);

  File file = fs.open(path, FILE_APPEND);
  if(!file){
    Serial.println("Failed to open file for appending");
    return;
  }
  if(file.print(message)){
      Serial.println("Message appended");
  } else {
    Serial.println("Append failed");
  }
  file.close();
}

void renameFile(fs::FS &fs, const char * path1, const char * path2){
  Serial.printf("Renaming file %s to %s\n", path1, path2);
  if (fs.rename(path1, path2)) {
    Serial.println("File renamed");
  } else {
    Serial.println("Rename failed");
  }
}

void deleteFile(fs::FS &fs, const char * path){
  Serial.printf("Deleting file: %s\n", path);
  if(fs.remove(path)){
    Serial.println("File deleted");
  } else {
    Serial.println("Delete failed");
  }
}

void testFileIO(fs::FS &fs, const char * path){
  File file = fs.open(path);
  static uint8_t buf[512];
  size_t len = 0;
  uint32_t start = millis();
  uint32_t end = start;
  if(file){
    len = file.size();
    size_t flen = len;
    start = millis();
    while(len){
      size_t toRead = len;
      if(toRead > 512){
        toRead = 512;
      }
      file.read(buf, toRead);
      len -= toRead;
    }
    end = millis() - start;
    Serial.printf("%u bytes read for %u ms\n", flen, end);
    file.close();
  } else {
    Serial.println("Failed to open file for reading");
  }


  file = fs.open(path, FILE_WRITE);
  if(!file){
    Serial.println("Failed to open file for writing");
    return;
  }

  size_t i;
  start = millis();
  for(i=0; i<2048; i++){
    file.write(buf, 512);
  }
  end = millis() - start;
  Serial.printf("%u bytes written for %u ms\n", 2048 * 512, end);
  file.close();
}

//END SD
